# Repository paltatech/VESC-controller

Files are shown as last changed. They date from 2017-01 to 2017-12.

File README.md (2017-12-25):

# 3 phase motor controller for high power systems
This is the hardware repository of a 3 phase inverter brain, UNTESTED but designed with the following specs in mind:

* Compatible with VESC firmware and software tools
* Embedded security features (overcurrent protection, pwm overlap elimination, etc)


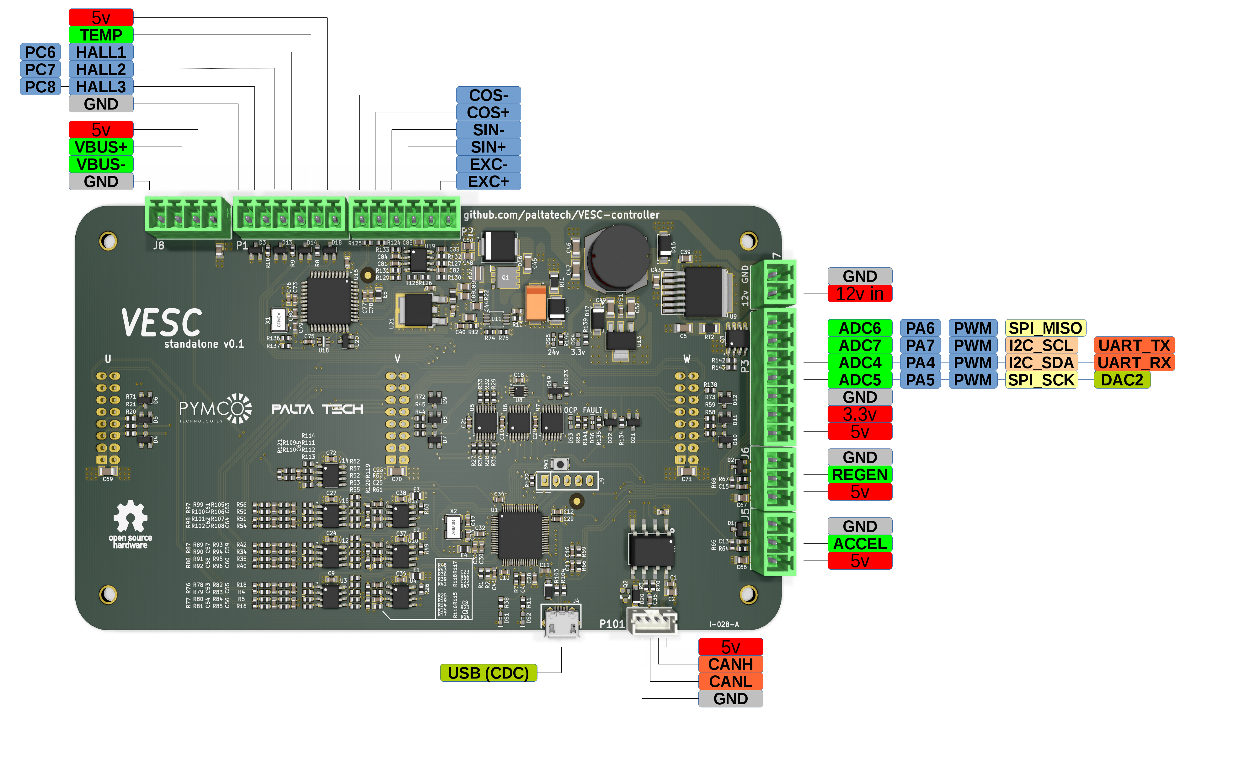
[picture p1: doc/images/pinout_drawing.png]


## Microcontroller
The core of the system is a 32 bit ARM Cortex M4 MCU (STM32F405) running ChibiOS RTOS.

## Communication interfaces
* CAN bus for control, configuration and monitoring
* USB for light usage, firmware upload/upgrade and configuration.
* UART, I2C and ADCs and GPIOs available

## Motor inputs
* Bus Voltage (differential)
* Phase current (differential)
* Phase voltage (differential)
* Gate driver fault
* Power_good from gate driver
* Motor temperature
* Hall/encoder
* Resolver

## Gate driver outputs
* PWM high/low
* dynamic gate drive current (pwm)
* 24v power

You can also check the layout [here](https://eyrie.io/board/6f397be723754f039735d8350260c2c0) 

Made open source with KiCAD, an open source EDA tool.

## Interface boards
This controller can be interfaced directly to a power stage, or through an interface board.
An example of interface board is at adaptor boards/power_integrations_2SP0115T2A/ and looks like this

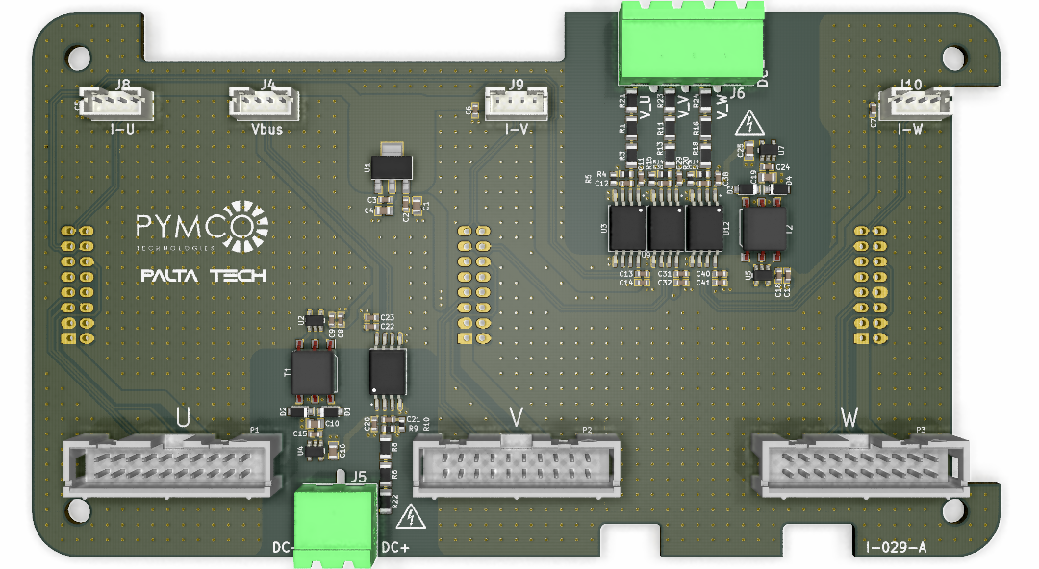
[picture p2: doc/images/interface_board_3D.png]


An example of system assembly is also included in this repository

## Control board setup

First you need to flash the VESC bootloader. To do so, connect a STLinkv2 to connector J9. In a Linux machine open a terminal and clone the bootloader repository:

1. `git clone git@github.com:vedderb/bldc-bootloader.git`
2. `cd bldc-bootloader`
3. `make upload`   <- this will compile and flash the bootloader

Next step is to flash the VESC firmware.

1. `git clone git@github.com:vedderb/bldc.git`
2. `Make sure you go to conf_general.h and uncomment the line #define HW_VERSION_PALTA. This will enable all the features especific to this high power control board.`
3. `Configure the DEADTIME required for your power switches, look for the line #define HW_DEAD_TIME_VALUE		181  // 1.4usec  in hw_palta.h`
4. `cd bldc`
5. `make upload`  <- this will compile and flash vesc firmware

Connect the board via USB (conn J4) and launch the latest [VESC-tool](http://vesc-project.com/vesc_tool).

1. Press the connect button (top right). The status bar should show your PALTA board connected.
2. Load a sample configuration for this board, you probably need to tune the deadtime compensation field.
3. Run the motor setup wizard.

## System setup

A high power controller would generally need a battery, wiring, contactor, DC link, gate drivers, switches, an interface board, 3 current sensors, a heatsink and a motor. Make sure you have everything you need and you understand all the connections and dangers involved, especially the safety related stuff.

## License
This documentation describes Open Hardware and is licensed under the CERN OHL v. 1.2

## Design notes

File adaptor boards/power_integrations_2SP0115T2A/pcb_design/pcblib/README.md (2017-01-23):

kicad-pcblib
============

(Warning: Work in progress!)

These are my KiCad PCB libraries, meant to be used with my schematic
libraries: https://github.com/cpavlina/kicad-schlib

IPC footprints
--------------

The IPC footprints are auto-generated from the FreePCB IPC libraries.
I used to require you to run 'make' to fetch them and convert them, but
FreePCB appears to be pretty solidly deceased now, so I'm including them
in my own library.

The FreePCB libraries are public domain (as clarified by FreePCB's creator,
contrary to the license of the software itself), and generated from IPC data.

If they ever do change and you want to rebuild them, here are the old instructions:

> Requires Make and Python 2.7+/3. Just run 'make ipc' after cloning this repository;
> the makefile will download the FreePCB IPC libraries and convert them to KiCad
> .pretty libs. Note that I am not distributing the FreePCB libraries, but I
> could; if they ever become unavailable I will add them here.

3D models
---------

The footprints reference [these nice 3D models](http://smisioto.no-ip.org/elettronica/kicad/kicad-en.htm).
There is a Python script to download and extract them; just run 'make 3d' to
run it.

They're pretty big, so please don't pull them repeatedly. Be nice to his server.

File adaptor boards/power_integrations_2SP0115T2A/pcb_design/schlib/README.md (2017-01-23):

kicad-schlib
============

(Warning: work in progress!)

These are my KiCad schematic libraries, meant to be used with my PCB
libraries:

https://github.com/cpavlina/kicad-pcblib

For preview renders, look here:

https://github.com/cpavlina/kicad-schlib-preview

Using these libraries
---------------------

This repository includes a script to create a KiCad project, at
[`create_project.sh`](https://raw.githubusercontent.com/cpavlina/kicad-schlib/master/create_project.sh),
to be called like this:

    create_project.sh  project_name

It will:

1. Create a directory called `project_name`
1. `git init` if not already in a git repository
1. Add `cpavlina/kicad-schlib` and `cpavlina/kicad-pcblib` as submodules, shallow-cloned to save space
1. Create the basic project files with all the libraries preloaded

The script doesn't depend on any other files in the repository, so you can
download and run only the script itself without having to clone the repository
yourself.

Why submodules?
---------------

Yeah, I know a lot of people don't like submods, but I find them just about
perfect for this application, for the following very important (IMHO) reason:

*Submodules link to a specific commit.* This is important when building a PCB.
KiCad does not version libraries, so without doing this, the libraries could
update underneath your project and introduce unnoticed errors. Using submodules
ties your project to the parts you initially started using, and if you want to
update (and have the time to review changes and make sure there are no errors),
you can do this manually.

When cloning a project using submodules, it is normally required to use `git
clone --recursive`; note that because KiCad cache the library parts that have
actually been used, a project will still be readable if the libraries aren't
also cloned (and can be distributed without them for reference purposes).

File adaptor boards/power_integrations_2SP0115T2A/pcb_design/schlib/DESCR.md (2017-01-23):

# Templates for part descriptions

## FPGA, CPLD, etc

`FPGA nLEs nIOs _RAM_ [footprint]`

`CPLD nLEs nIOs [footprint]`

- nLEs: Number of logic elements. `LEs:4608`
- nIOs: Number of IO pins. `IOs:142`
- RAM: Amount of RAM in metric kbits. `RAM:120kb`

These chips can differ significantly from each other, so just use common sense.

## A/D converters

`ADC.n nbit sps interface _inl_ _dnl_ _refppm_ [footprint]`

- sps: Samples per second. `50kSa/s` Alternatively: settling time. `15µs`
- interface: data interface (SPI, I2C, parallel, etc)
- inl: Integral nonlinearity, LSB. `INL:2`
- dnl: Differential nonlinearity, LSB. `DNL:3`
- refppm: PPM/K of integrated reference, if present. `Ref:2ppm/K`

## D/A converters

`DAC.n nbit sps interface _inl_ _dnl_ _refppm_ [footprint]`

- sps: Samples per second. `50kSa/s` Alternatively: settling time. `15µs`
- interface: data interface (SPI, I2C, parallel, etc)
- inl: Integral nonlinearity, LSB. `INL:2`
- dnl: Differential nonlinearity, LSB. `DNL:3`
- refppm: PPM/K of integrated reference, if present. `Ref:2ppm/K`

## Linear regulators, LDOs, DC-DC

`Reg Lin voltage current [footprint]`

`Reg LDO voltage current [footprint]`

`Reg Buck in:vin vout current freq [footprint]`

`Reg Boost in:vin vout current freq [footprint]`

Also RegCtrlr.

- voltage: output voltage or AdjV
- current: maximum output current or AdjI

The cutoff for linear vs. LDO is suggested to be a typical dropout of 1.2V at full load.
This places the worst IC commonly considered "LDO" (LM1117) just inside the LDO category.

## Voltage references

`VRef Series/Shunt voltage tolerance ppm/K [footprint]`

## Logarithmic amplifiers, detectors

`LogAmp dynamic_range bandwidth [footprint]`

`LogDetect dynamic_range bandwidth [footprint]`

The distiction is that detectors typically have an integrated low-pass filter, so
high RF comes out as a DC power level.

## Comparators

`Comp.n _delay_ _irange_ _outtech_ _extras_ [footprint]`

- .n: number of units. omit if one.
- delay: propagation delay, ns.
- irange: RRI, SSI, OverTopI
- outtech: OpenDrain, OpenColl, TTL, CMOS, LVDS, etc.
- extras: ProgHysteresis, etc.

## Operational amplifiers, instrumentation amplifiers

`OpAmp.n _intype_ GBW _slewrate_ _iorange_ _tech_ _extras_ [footprint]`

`InAmp.n _intype_ GBW _slewrate_ _iorange_ _tech_ _extras_ [footprint]`

- .n: number of units. omit if one.
- intype:
  - VFB for voltage feedback, but omit for GBW < 75 MHz
  - CFA for current feedback
- slewrate:
  - Only specify if notable (suggested cutoff: 6V * GBW)
  - Always specified in V/µs
- iorange:
  - RRI, RRO, RRI RRO if rail-to-rail (go by manufacturer's claims)
  - SSI, SSO, SSIO if single-supply
  - OverTopI if over-the-top
  - OpenCollO, OpenDrnO if open-collector/open-drain
- tech: input circuit technology. CMOS, JFET, etc. Omit for BJT or if unspecified.
- extras:
  - LowVos: low V offset (suggested: < 1mV)
  - VLowVos: very low V offset (suggested: < 50µV)
  - LowIB: low input bias current (suggested: < 1µA)
  - VLowIB: very low input bias current (suggested: < 1 nA)
  - LowNoise: low noise (cutoff depends on applications!)
  - Chopper: chopper-stabilized

## Discrete transistors

`PMOS.n _semi_ -xV -xA _Rdson_ _Vgsth_ [footprint]`

`NMOS.n _semi_ xV xA _Rdson_ _Vgsth_ [footprint]`

`PNP.n _semi_ -xV -xA _Pd_ _ft_ [footprint]`

`NPN.n _semi_ xV xA _Pd_ _ft_ [footprint]`

`NJF.n _semi_ xV Idss [footprint]`

`PJF.n _semi_ xV Idss [footprint]`

`SCR xV xA _Itsm_ [footprint]`

`PUT xV xW _Itrm_ [footprint]`

`UJT xV xW [footprint]`

- semi: specify semiconductor material for exotic devices
- Use negative voltage, current for P-type devices
- Rdson: on-resistance of MOSFET. `34mR`
- Vgsth: threshold of MOSFET. Typically at a low current like 250µA. Negative for P-type. `-3Vth`

## Discrete diodes

`Diode xV xA [footprint]`

`Schottky xV xA [footprint]`

`Zener xV xW Iz:xA [footprint]`

`TVS xV _pulse_ _Cj_ [footprint]`

`Varicap xV Cjrange [footprint]`

`LED color wavelength xV xA [footprint]`

- pulse: 8/20µs peak pulse

## Optocouplers

`Optocoup NPN+base isoV fwdcurrentA vvvVceo [footprint]`

## Microcontrollers

`MCU nbit/arch ROM:nKB RAM:nKB _extras_ [footprint]`

- arch: for ARM, use such as ARM-M4
- extras: list features not including the usuals like SPI/I2C/UART.

## Passives

`IND nH nR _SRF:100MHz_ _(dimensions)_ _[footprint]_`

## Digital interface converters

`Interface FROM TO [footprint]`

## Digital attenuators

`Atten ndB nbit BW _tech_ [footprint]`

- tech: device/semiconductor technology, if appropriate

## Analog switch

`AnSwitch nPnT _tech_ _extras_ [footprint]`

## Memories

`Mem type size interface _speed_ [footprint]`

- type: EEPROM, Flash, SRAM, DRAM, DDR2-SDRAM, etc
- size: use B for byte, bit for bit
- speed: either interface clock or access time

## Temperature sensors

`Sensor Temp range accuracy interface [footprint]`

- range: only specified range (not absolute max): `0-70C`
- accuracy: `±2C`
- interface: can be `Analog`

## Digital drivers, level shifters, translators

`Logic BusTXRX width supplyrange/techs speed features [footprint]`

`Logic LevelShift width supplyrange/techs speed features [footprint]`

`Logic TXRX supplyrange/techs speed features [footprint]`

`Logic TX supplyrange/techs speed features [footprint]`

`Logic RX supplyrange/techs speed features [footprint]`

`Logic Isolator supplyrange speed isolation features [footprint]`

## Oscillators, PLL

`Osc freq _tech_ outtype extras [footprint]`

`PLL freqmax outtype extras [footprint]`

`OscPLL freqmax outtype extras [footprint]`

- tech: oscillator technology (Crystal, CMEMS, etc)

## Power drivers

`Driver type nchannels tech powerlevel interface [footprint]`

## Displays

`Display VFD 7seg Digits:8 Muxed`

`Display LED 7seg Digits:3 Muxed Green`

## Modulators, Demodulators

`ModDemod freq (type) [footprint]`

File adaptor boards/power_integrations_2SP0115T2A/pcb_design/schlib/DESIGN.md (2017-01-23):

# Design Guidelines

## General

- Descriptions are standardized for simple searching. See DESCR.md. If you want to add a new class of part that doesn't have an entry in DESCR.md, please contribute to that file as well.
- Separate power units: orient vertically, pins at +/- 0.4in with 0.15in length
- Text should be 50 mil in general
- Pin length, numbering, general naming:

    - ICs: pins at least 0.15in long, pin numbers 50 mil text
    - Discrete semis: pin numbers 40 mil text.
    - Passives: omit pin numbers for two-pin parts. Three-pin parts can omit numbers when the third pin is structural (e.g. grounded crystal). When using numbers, use 40 mil text.
    - Name all pins. Hide names when the symbol graphic identifies the pin instead (transistor BCE, etc)
    - Prefer overbar for inverted pins with names, inversion circle for inverted pins without names. Don't combine the two!

- In manufacturer libraries, name parts according to manufacturer naming scheme.
- One footprint per part; specify footprint in Footprint field
- For parts with a large number of variants (e.g. fixed-voltage regulators), a placeholder in the name is acceptable: LM1117DT-v.v
- Prefer logical schematic to blank parts with names - e.g., use buffer symbol in buffers, not just pins named IN and OUT.
- Include [bomtool](https://github.com/cpavlina/bomtool) BOM lines whenever possible.
- Do not duplicate data! Don't fill in footprint filters, we use the footprint *field*. Don't use the keywords field, the new component chooser filters on description.

## Power supply naming

- Do not follow manufacturer naming. Be consistent, Microchip's "VSS" is no different from Atmel's "GND".
- For single rail parts, name main supply V+ (not VCC, VDD)
- For multi-rail parts, name main supply according to use when possible (VCORE, not V1.2)
- Ground is GND, not VSS

## Template parts

- Template libraries are prefixed with an underscore (`_passive`, `_semi`)
- Do not include footprints

## Very large logic (FPGA, large MCU, etc)

- Use "bracketed" multi-part style (see Altera library for an example)

## Small logic (7400, etc)

- Use traditional (non-IEC) symbols for very simple like NAND
- Use IEC or IEC-like symbols for more complex like shift register
- Use separate power units

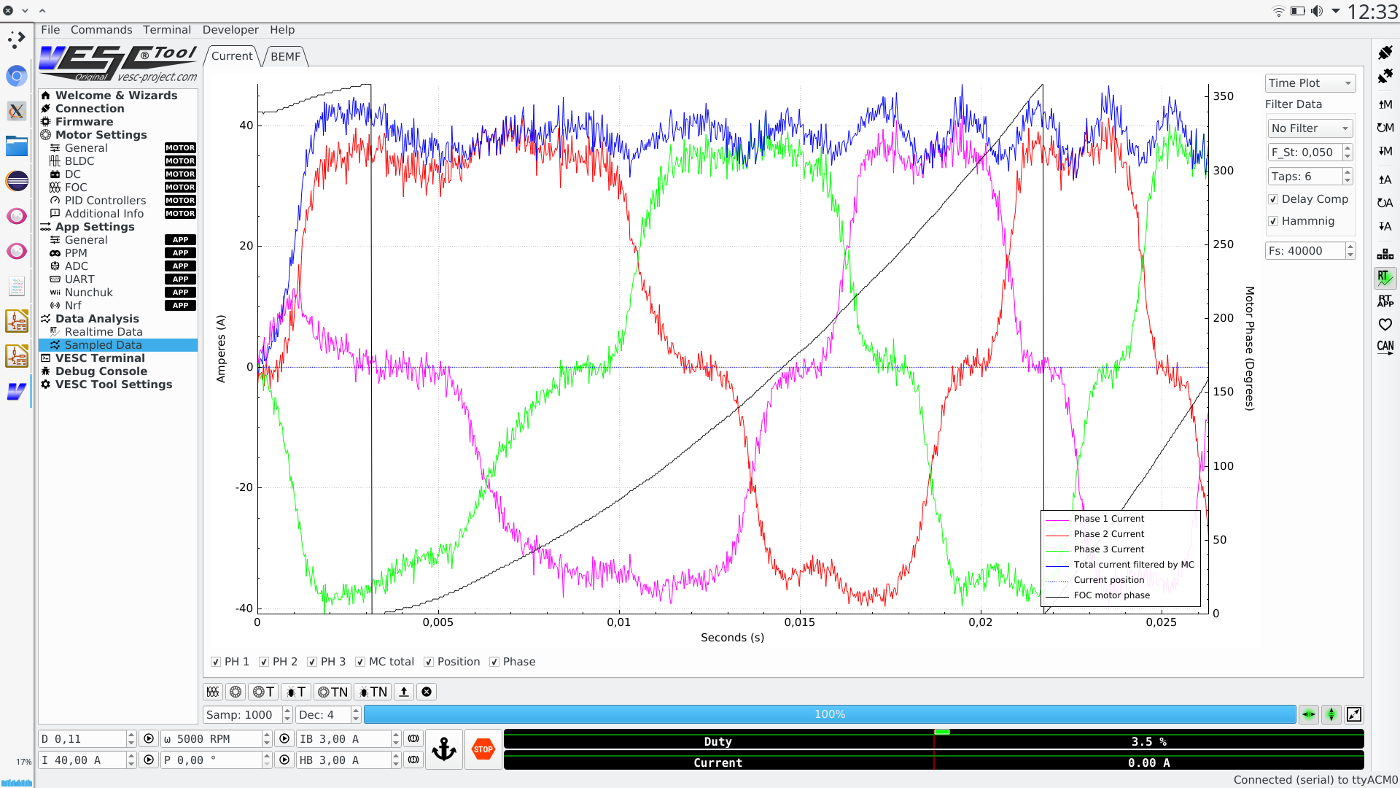
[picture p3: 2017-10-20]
adaptor boards/power_integrations_2SP0115T2A/doc/startup with 1.4usec DT.png

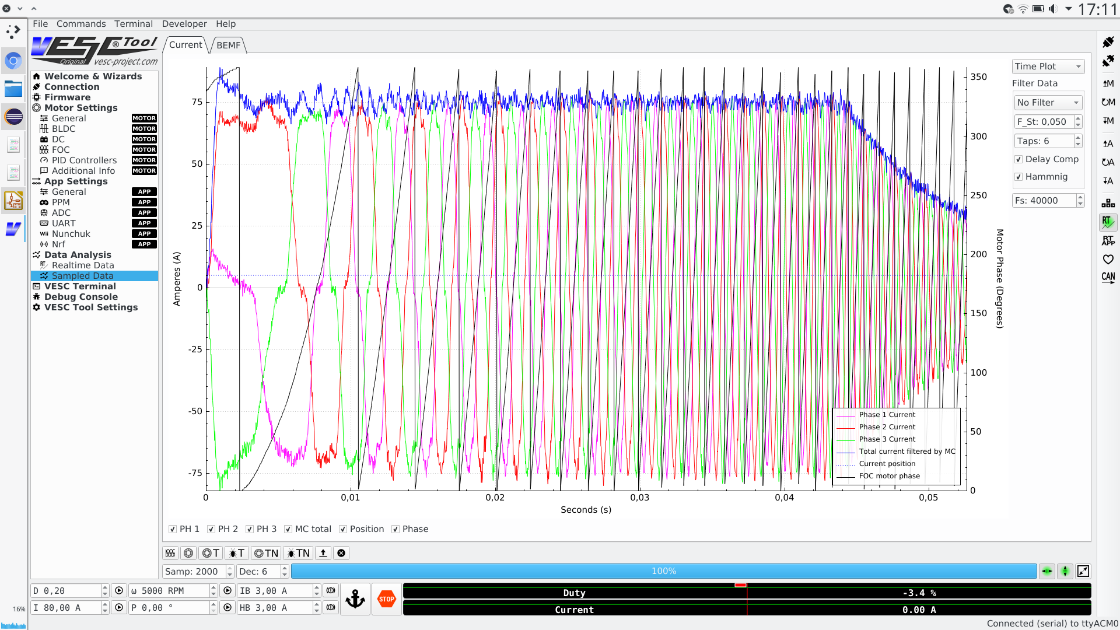
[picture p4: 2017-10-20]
adaptor boards/power_integrations_2SP0115T2A/doc/startup with 1.4usec DT 80A.png

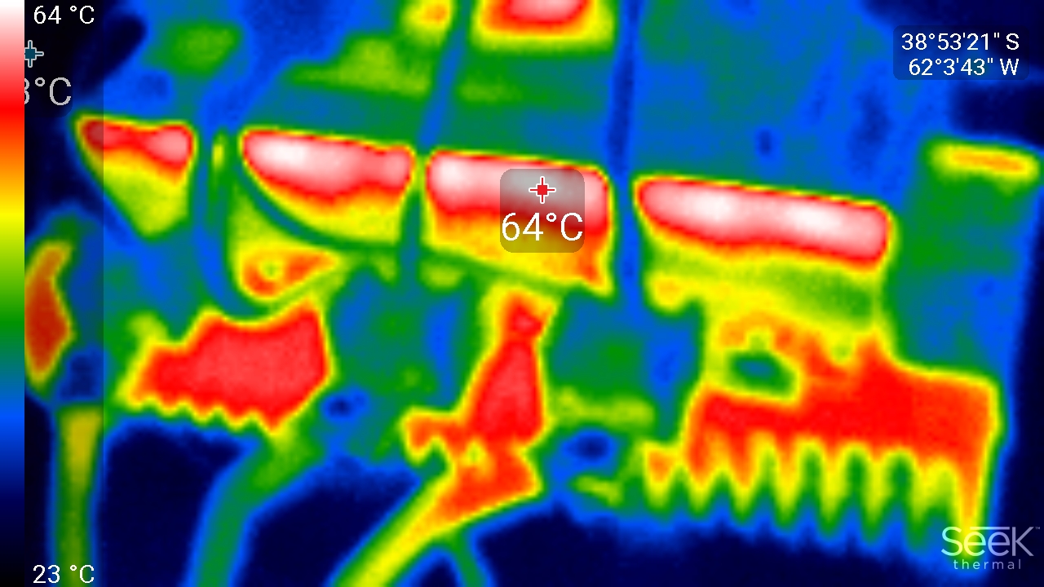
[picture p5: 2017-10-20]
adaptor boards/power_integrations_2SP0115T2A/doc/img_thermal_1497133271852.jpg

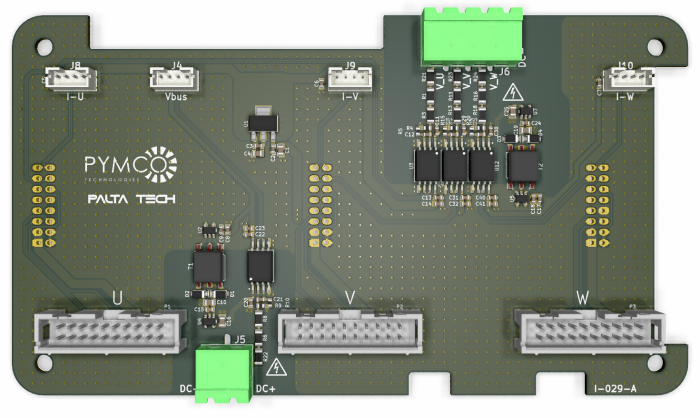
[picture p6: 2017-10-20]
adaptor boards/power_integrations_2SP0115T2A/doc/interface board v0.1.png

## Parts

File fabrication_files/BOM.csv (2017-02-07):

Refs | Value | Footprint | QTY | MFR | MPN | SPR | SPN
RT1 | FUSE 5A SLOW | IPC7351-Most:RESC3216X60 | 1 | Bel Fuse Inc. | C1S 5 | Digikey | 507-1194-1-ND
RT2 | POLYFUSE 1A | IPC7351-Most:RESC3216X60 | 1 | Bel Fuse Inc. | 0ZCJ0050AF2E | Digikey | 507-1803-1-ND
C401;C1;C35;C18;C21;C20;C19;C74;C73;C77;C82;C81;C85;C75;C87;C86;C51;C13;C13;C32;C30;C34;C10;C11;C12;C3;C9;C36;C3;C9;C36;C3;C9;C36;C72 | 100nF | IPC7351-Nominal:CAPC1608X55 | 35 | Murata Electronics North America | GRM188R71E104KA01D | Digikey | 490-1524-1-ND
C8;C8;C8;C65 | 100pF | IPC7351-Nominal:CAPC1608X55 | 4 | KEMET | C0603C101J5GACTU | Digikey | 399-1061-1-ND
C83;C84 | 120pF | IPC7351-Nominal:CAPC1608X55 | 2 | KEMET | C0603C121F5GACTU | Digikey | 399-7850-1-ND
C79;C80;C17;C33 | 15pF | IPC7351-Nominal:CAPC1608X55 | 4 | Murata Electronics North America | GCM1885C1H150JA16D | Digikey | 490-4957-1-ND
C40;C42 | 180nF | IPC7351-Nominal:CAPC1608X55 | 2 | Murata Electronics North America | GRM188R71E184KA88D | Digikey | 490-6431-1-ND
C14;C14 | 1nF | IPC7351-Nominal:CAPC1608X55 | 2 | Murata Electronics North America | GRM188R71H102KA01D | Digikey | 490-1494-1-ND
C53;C54;C53;C54;C53;C54 | 2.2nF | IPC7351-Nominal:CAPC1608X55 | 6 | Murata Electronics North America | GRM188R71H222KA01D | Digikey | 490-1500-1-ND
C76;C78;C41;C31;C28;C29;C4 | 2.2uF | IPC7351-Nominal:CAPC1608X55 | 7 | Murata Electronics North America | GRM188R71A225KE15D | Digikey | 490-4520-1-ND
C55;C56;C55;C56;C55;C56 | 220pF | IPC7351-Nominal:CAPC1608X55 | 6 | Murata Electronics North America | GRM1885C1H221JA01D | Digikey | 490-1435-1-ND
R37 | 18mOhm | IPC7351-Nominal:CAPC1632X76 | 1 | Susumu | PRL1632-R018-F-T1 | Digikey | PRL1632.018FCT-ND
C39;C43 | 1uF 50v | IPC7351-Nominal:CAPC2012X70 | 2 | Taiyo Yuden | UMK212B7105KG-T | Digikey | UMK212B7105KG-T
C88;C89;C48;C50 | 22uF | IPC7351-Nominal:CAPC2012X70 | 4 | TDK Corporation | C2012X5R1V226M125AC | Digikey | 445-14428-1-ND
C2;C68;C66;C67 | 4.7uF | IPC7351-Nominal:CAPC2012X70 | 4 | Murata Electronics North America | GRM21BR71A475KA73K | Digikey | 490-6479-1-ND
C44 | 680pF | IPC7351-Nominal:CAPC2012X70 | 1 | Samsung Electro-Mechanics America, Inc. | CL21C751JBCNNNC | Digikey | 1276-2691-1-ND
C7 | 750pF | IPC7351-Nominal:CAPC2012X70 | 1 | Samsung Electro-Mechanics America, Inc. | CL21C751JBCNNNC | Digikey | 1276-2691-1-ND
C5 | 10uF 35v | IPC7351-Nominal:CAPC3216X70 | 1 | Taiyo Yuden | GMK316AB7106KL-TR | Digikey | 587-3007-1-ND
C45 | 2.2uF 50v | IPC7351-Nominal:CAPC3216X70 | 1 | Murata Electronics North America | GRM31CR71H225KA88L | Digikey | 490-3367-1-ND
C46;C47;C49;C52 | 22uF 10v | IPC7351-Nominal:CAPC3216X70 | 4 | Taiyo Yuden | LMK316AB7226ML-TR | Digikey | 587-2782-1-ND
C71;C70;C69 | 4.7uF 50v | IPC7351-Nominal:CAPC3216X70 | 3 | Murata Electronics North America | GRM31CR71H475KA12L | Digikey | 490-6521-1-ND
C6 | 4.7uF 50v tant | IPC7351-Nominal:CAPMP7343X310 | 1 | Vishay Sprague | 593D475X9050D2TE3 | Digikey | 718-1107-1-ND
D15;D17 | SS16 | IPC7351-Nominal:DIOM5326X292 | 2 | Fairchild/ON Semiconductor | SS16 | Digikey | SS16FSCT-ND
D16 | 30BQ100TR | IPC7351-Nominal:DIOM7959X265 | 1 | SMC Diode Solutions | 30BQ100TR | Digikey | 1655-1389-1-ND
E5;E6;E4;E1;E1;E1 | BEAD-220ohm@100khz | IPC7351-Nominal:INDC2012X130 | 6 | Murata Electronics North America | BLM21PG221SN1D | Digikey | 490-1054-1-ND
L1;L3 | 22uH 5.2A | IPC7351-Nominal:INDC3225X135 | 2 | Bourns Inc. | SRR1210-220M | Digikey | SRR1210-220MCT-ND
X1;X2 | ABM3B - 8MHz | IPC7351-Nominal:OSCCC320X500X150 | 2 | Abracon LLC | ABM3B-8.000MHZ-10-1UT | Digikey | 535-9721-1-ND
U1 | STM32F40X_LQFP64 | IPC7351-Nominal:QFP50P1200X1200X100-64 | 1 | STMicroelectronics | STM32F405RGT6 | Digikey | 497-11767-ND
U15 | AD2S1205 | IPC7351-Nominal:QFP80P1200X1200X160-44 | 1 | Analog Devices Inc. | AD2S1205YSTZ | Digikey | AD2S1205YSTZ-ND
R136;R137;R6 | 0R | IPC7351-Nominal:RESC1608X50 | 3 | Yageo | RC0603JR-070RL | Digikey | 311-0.0GRCT-ND
R12 | 1.78k | IPC7351-Nominal:RESC1608X50 | 1 | Yageo | RC0603FR-071K78L | Digikey | 311-1.78KHRCT-ND
R86;R141;R22;R78;R79;R80;R81;R78;R79;R80;R81;R38;R11;R135;R134;R78;R79;R80;R81 | 100R | IPC7351-Nominal:RESC1608X50 | 19 | Yageo | RC0603FR-07100RL | Digikey | 311-100HRCT-ND
R65;R65 | 100k | IPC7351-Nominal:RESC1608X50 | 2 | Yageo | RC0603FR-07100KL | Digikey | 311-100KHRCT-ND
R138;R126;R130;R128;R131;R75;R143;R142;R2;R10;R9;R8;R7;R18;R16;R19;R17;R25;R24;R18;R16;R19;R17;R25;R24;R140;R18;R16;R19;R17;R25;R24;R111;R112;R114;R113 | 10k | IPC7351-Nominal:RESC1608X50 | 36 | Yageo | RC0603FR-0710KL | Digikey | 311-10.0KHRCT-ND
R132;R133 | 15.4k | IPC7351-Nominal:RESC1608X50 | 2 | Yageo | RC0603FR-0715K4L | Digikey | 311-15.4KHRCT-ND
R74 | 180k | IPC7351-Nominal:RESC1608X50 | 1 | Yageo | RC0603FR-07180KL | Digikey | 311-180KHRCT-ND
R64;R64;R122;R23;R82;R83;R84;R85;R116;R115;R23;R82;R83;R84;R85;R116;R115;R139;R23;R82;R83;R84;R85;R116;R115 | 1k | IPC7351-Nominal:RESC1608X50 | 25 | Yageo | RC0603FR-071KL | Digikey | 311-1.00KHRCT-ND
R123;R20;R21;R71;R20;R21;R71;R103;R104;R20;R21;R71 | 22R | IPC7351-Nominal:RESC1608X50 | 12 | Yageo | RC0603FR-0722RL | Digikey | 311-22.0HRCT-ND
R127;R129 | 22k | IPC7351-Nominal:RESC1608X50 | 2 | Yageo | RC0603FR-0722KL | Digikey | 311-22.0KHRCT-ND
R66;R66 | 270k | IPC7351-Nominal:RESC1608X50 | 2 | Yageo | RC0603FR-07270KL | Digikey | 311-270KHRCT-ND
R76;R77;R76;R77;R76;R77;R121 | 2k | IPC7351-Nominal:RESC1608X50 | 7 | Yageo | RC0603FR-072KL | Digikey | 311-2.00KHRCT-ND
R13 | 33.2k | IPC7351-Nominal:RESC1608X50 | 1 | Yageo | RC0603FR-0733K2L | Digikey | 311-33.2KHRCT-ND
R30;R27;R31;R28;R32;R29;R33;R26;R26;R26;R109;R110 | 4.7k | IPC7351-Nominal:RESC1608X50 | 12 | Yageo | RC0603FR-074K7L | Digikey | 311-4.70KHRCT-ND
R3;R70 | 60.4R | IPC7351-Nominal:RESC1608X50 | 2 | Yageo | RC0603FR-0760R4L | Digikey | 311-60.4HRCT-ND
R124;R125 | 68.1k | IPC7351-Nominal:RESC1608X50 | 2 | Yageo | RC0603FR-0768K1L | Digikey | 311-68.1KHRCT-ND
R4;R5;R14;R15;R4;R5;R14;R15;R4;R5;R14;R15 | 8.87k | IPC7351-Nominal:RESC1608X50 | 12 | Yageo | RC0603FR-078K87L | Digikey | 311-8.87KHRCT-ND
R1 | NTC 10k | IPC7351-Nominal:RESC1608X50 | 1 | Murata Electronics North America | NCP18XH103F03RB | Digikey | 490-4800-1-ND
U19 | AD8397 | IPC7351-Nominal:SOIC127P600X175-8 | 1 | Analog Devices Inc. | AD8397ARZ | Digikey | AD8397ARZ-ND
Q3 | AO4805 | IPC7351-Nominal:SOIC127P600X175-8 | 1 | Alpha & Omega Semiconductor Inc. | AO4805 | Digikey | 785-1055-1-ND
U4;U4;U4 | LM2903DT | IPC7351-Nominal:SOIC127P600X175-8 | 3 | STMicroelectronics | LM2903DT | Digikey | 497-1559-1-ND
U3;U3;U3;U14 | OPA2376AIDR | IPC7351-Nominal:SOIC127P600X175-8 | 4 | Texas Instruments | OPA2376AIDR | Digikey | 296-22564-1-ND
U8 | SN74AUP1G74 | IPC7351-Nominal:SOP50P310X100-8 | 1 | Texas Instruments | SN74AUP1G74DCUR | Digikey | 296-19761-1-ND
U11 | LM3488 | IPC7351-Nominal:SOP65P490X109-8 | 1 | Texas Instruments | LM3488MM/NOPB | Digikey | LM3488MM/NOPBCT-ND
U5 | 7400-TSSOP | IPC7351-Nominal:SOP65P640X110-14 | 1 | Texas Instruments | SN74LVC00APWR | Digikey | 296-1216-1-ND
U6;U7 | SN74ACT08PWR | IPC7351-Nominal:SOP65P640X110-14 | 2 | Texas Instruments | SN74ACT08PWR | Digikey | 296-4355-1-ND
J9 | SWD | conn-100mil:CONN-100MIL-M-1x5 | 1
J1 | GATE_DRIVER_CONN_U | conn-100mil:CONN-100MIL-M-2x8 | 1 | Amphenol FCI | 67997-216HLF | Digikey | 609-3238-ND
J2 | GATE_DRIVER_CONN_V | conn-100mil:CONN-100MIL-M-2x8 | 1 | Amphenol FCI | 67997-216HLF | Digikey | 609-3238-ND
J3 | GATE_DRIVER_CONN_W | conn-100mil:CONN-100MIL-M-2x8 | 1 | Amphenol FCI | 67997-216HLF | Digikey | 609-3238-ND
J4 | micro USB | conn-fci:CONN-10118194-0001LF-FCI | 1 | Amphenol FCI | 10118194-0001LF | Digikey | 609-4618-1-ND
J7 | 12V | conn-phoenix:mcv_1,5-2-G-3,81 | 1 | Phoenix Contact | 1803426 | Digikey | 277-1221-ND
J5 | ACCEL | conn-phoenix:mcv_1,5-3-G-3,81 | 1 | Phoenix Contact | 1803439 | Digikey | 277-1222-ND
J6 | REGEN | conn-phoenix:mcv_1,5-3-G-3,81 | 1 | Phoenix Contact | 1803439 | Digikey | 277-1222-ND
J8 | V_BUS | conn-phoenix:mcv_1,5-4-G-3,81 | 1 | Phoenix Contact | 1803442 | Digikey | 277-1223-ND
P1 | HALL/Encoder | conn-phoenix:mcv_1,5-6-G-3,81 | 1 | Phoenix Contact | 1803468 | Digikey | 277-1225-ND
P2 | Resolver | conn-phoenix:mcv_1,5-6-G-3,81 | 1 | Phoenix Contact | 1803468 | Digikey | 277-1225-ND
P3 | PWR_COMM | conn-phoenix:mcv_1,5-7-G-3,81 | 1 | Phoenix Contact | 1803471 | Digikey | 277-1226-ND
L2 | 27uH | manuf:BOURNS-SDR1307 | 1 | Bourns Inc. | SDR1307-270ML | Digikey | SDR1307-270MLCT-ND
Q1 | BSC340N08 | manuf:TEXAS-Q5A | 1 | Infineon Technologies | BSC340N08NS3GATMA1 | Digikey | BSC340N08NS3GATMA1CT-ND
U9 | LM22676QTJ-5.0 | manuf:TO-263-7-TEXAS | 1 | Texas Instruments | LM22676QTJE-5.0/NOPB | Digikey | LM22676QTJE-5.0/NOPBCT-ND
SW1 | BOOTLOADER | paltatech:SMD-Switch_B3U-1000-B | 1 | Omron Electronics Inc-EMC Div | B3U-1000P | Digikey | SW1020CT-ND
U2 | ISO1050 | paltatech:SO8-ISO1050 | 1 | Texas Instruments | ISO1050DUBR | Digikey | 296-24818-1-ND
DS6 | FAULT | smd-semi:LED-0603 | 1 | Lite-On Inc. | LTST-C191KRKT | Digikey | 160-1447-1-ND
DS2;DS4 | GREEN | smd-semi:LED-0603 | 2 | Lite-On Inc. | LTST-C191KGKT | Digikey | 160-1446-1-ND
DS3 | OCP | smd-semi:LED-0603 | 1 | Lite-On Inc. | LTST-C191KRKT | Digikey | 160-1447-1-ND
DS1;DS5 | RED | smd-semi:LED-0603 | 2 | Lite-On Inc. | LTST-C191KRKT | Digikey | 160-1447-1-ND
Q2 | 2N7002PW | smd-semi:SC-70 | 1 | Nexperia USA Inc. | 2N7002PW,115 | Digikey | 568-5987-1-ND
U18 | SN74LVC1G | smd-semi:SC-70-6 | 1 | Texas Instruments | SN74LVC1G11IDCKRQ1 | Digikey | 296-36722-1-ND
D20 | MBR0540 | smd-semi:SOD-123 | 1 | Fairchild/ON Semiconductor | MBR0540 | Digikey | MBR0540CT-ND
U13 | LM1117IMP-v.v | smd-semi:SOT-223 | 1 | Texas Instruments | LM1117IMP-3.3/NOPB | Digikey | LM1117IMP-3.3/NOPBCT-ND
U20 | APX809 | smd-semi:SOT-23 | 1 | Diodes Incorporated | APX809-46SRG-7 | Digikey | APX809-46SRGDICT-ND
D19;D1;D1;D3;D13;D14;D18;D4;D5;D6;D4;D5;D6;D22;D21;D4;D5;D6 | BAT54S | smd-semi:SOT-23 | 18 | Toshiba Semiconductor and Storage | TBAT54S,LM | Digikey | TBAT54SLMCT-ND
U21 | NCV78Mxx | smd-semi:TO-252 | 1 | ON Semiconductor | NCV78M12BDTRKG | Digikey | NCV78M12BDTRKGOSCT-ND
P101 | CANBUS | w_conn_jst-ph:b4b-ph-kl | 1 | JST Sales America Inc. | B4B-PH-K-S(LF)(SN) | Digikey | 455-1706-ND
DZ1 | 1SMB18CAT | w_smd_diode:do214aa | 1 | ON Semiconductor | 1SMB18CAT3G | Digikey | 1SMB18CAT3GOSCT-ND

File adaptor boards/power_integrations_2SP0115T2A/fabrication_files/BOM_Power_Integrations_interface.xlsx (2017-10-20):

 |  |  |  |  |  |  | Board Qty: | 10
 |  |  |  |  |  |  | Total Cost: | $1107.35 |  |  |  | $547.41 |  |  |  |  |  | $442.05 |  |  |  |  |  | $892.66 |  |  |  |  |  | $507.91 |  |  |  |  |  | $2786.40
 |  |  |  |  |  |  | Unit Cost: | $110.74
Global Part Info |  |  |  |  |  |  |  |  | Digi-Key |  |  |  |  |  | Farnell |  |  |  |  |  | Mouser |  |  |  |  |  | Newark |  |  |  |  |  | Rs Components
Refs | Value | Desc | Footprint | Manf | Manf# | Qty | Unit$ | Ext$ | Avail | Purch | Unit$ | Ext$ | Cat# | Doc | Avail | Purch | Unit$ | Ext$ | Cat# | Doc | Avail | Purch | Unit$ | Ext$ | Cat# | Doc | Avail | Purch | Unit$ | Ext$ | Cat# | Doc | Avail | Purch | Unit$ | Ext$ | Cat# | Doc
P1-P3 | 2SP0115T_conector |  | conn-100mil:CONN-100MIL-F-2x10 | Amphenol FCI | 75869-104LF | 30 | $0.97 | $29.21 | 1894 |  | $1.20 | $35.85 | 609-1776-ND | Link (http://www.digikey.com/scripts/DkSearch/dksus.dll?WT.z_header=search_go&lang=en) |  |  | $0.97 | $29.21 | 1103952 | Link (http://it.farnell.com/webapp/wcs/stores/servlet/Search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) | 481 |  | $1.08 | $32.40 | 649-75869-104LF | Link (http://www.mouser.com/Search/Refine.aspx?Keyword=75869-104LF%20) |  |  | $1.01 | $30.30 | 93K5090 | Link (http://www.newark.com/webapp/wcs/stores/servlet/Search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) | 150 |  | $1.00 | $29.98 | 673-7600 | Link (http://it.rs-online.com/web/c/?searchTerm=75869-104LF%20)
R2,R7,R12,R17 | 20k |  | IPC7351-Nominal:RESC6432X70 |  | CRCW251220K0JNEG | 40 | $0.13 | $5.10 | 12547 |  | $0.35 | $13.92 | 541-20KXCT-ND | Link (http://www.digikey.com/product-detail/en/vishay-dale/CRCW251220K0JNEG/541-20KXCT-ND/1178612) |  |  | $0.17 | $6.93 | 1571740 | Link (http://it.farnell.com/webapp/wcs/stores/servlet/Search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) | 1615 |  | $0.22 | $8.64 | 71-CRCW2512J-20K-E3 | Link (http://www.mouser.com/ProductDetail/Vishay/CRCW251220K0JNEG/) |  |  | $0.18 | $7.40 | 89M6939 | Link (http://www.newark.com/webapp/wcs/stores/servlet/Search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) |  |  | $0.13 | $5.10 | 842-9496 | Link (http://it.rs-online.com/web/c/?searchTerm=CRCW251220K0JNEG%20)
U3,U6,U9,U12 | AMC1301 |  | IPC7351-Nominal:SOIC127P1032X265-8 | Texas Instruments | AMC1301DWVR | 40 | $5.65 | $226.04 | 3988 |  | $5.65 | $226.04 | 296-44577-1-ND | Link (http://www.digikey.com/product-detail/en/texas-instruments/AMC1301DWVR/296-44577-1-ND/6131178) |  |  | $5.74 | $229.61 | 2617071 | Link (http://it.farnell.com/texas-instruments/amc1301dwvr/amp-isolamento-210khz-50uv-soic/dp/2617071) |  |  |  |  |  |  |  |  | $7.03 | $281.20 | 96Y8999 | Link (http://www.newark.com/webapp/wcs/stores/servlet/Search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)
C11,C20,C29,C38 | 100nF |  | IPC7351-Nominal:CAPC1608X55 | Murata Electronics North America | GRM188R71E104KA01D | 40 | $0.02 | $0.77 | 9708975 |  | $0.09 | $3.44 | 490-1524-1-ND | Link (http://www.digikey.com/product-detail/en/murata-electronics-north-america/GRM188R71E104KA01D/490-1524-1-ND/587865) |  |  |  |  | 1828899 | Link (http://it.farnell.com/murata/grm188r71e104ka01d/condensatore-mlcc-x7r-100nf-25v/dp/1828899) |  |  |  |  |  |  |  |  |  |  | 14T3317 | Link (http://www.newark.com/murata/grm188r71e104ka01d/capacitor-ceramic-0-1uf-10-25v/dp/14T3317) |  |  | $0.02 | $0.77 | 723-5638 | Link (http://it.rs-online.com/web/c/?searchTerm=GRM188R71E104KA01D%20)
U4,U7 | TPS76350 |  | smd-semi:SOT-23-5 | Texas Instruments | TPS76350DBVR | 20 | $0.76 | $15.26 | 2878 |  | $0.86 | $17.14 | 296-2707-1-ND | Link (http://www.digikey.com/product-detail/en/texas-instruments/TPS76350DBVT/296-2707-1-ND/381498) |  |  | $0.81 | $16.22 | 2764732 | Link (http://it.farnell.com/webapp/wcs/stores/servlet/Search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) |  |  |  |  |  |  |  |  | $0.76 | $15.26 | 77C1037 | Link (http://www.newark.com/webapp/wcs/stores/servlet/Search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) |  |  |  |  | 661-4242 | Link (http://it.rs-online.com/web/p/regolatori-di-tensione-low-dropout/6614242/)
J3 | GATE_DRIVER_CONN_W |  | conn-100mil:CONN-100MIL-M-2x8 | Amphenol FCI | 87606-308LF | 10 | $1.77 | $17.70 | 1177 |  | $1.97 | $19.65 | 609-3554-ND | Link (http://www.digikey.com/scripts/DkSearch/dksus.dll?WT.z_header=search_go&lang=en) |  |  | $2.00 | $19.98 | 1278235 | Link (http://it.farnell.com/webapp/wcs/stores/servlet/Search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) | 346 |  | $1.77 | $17.70 | 649-87606-308LF | Link (http://www.mouser.com/Search/Refine.aspx?Keyword=87606-308LF%20) |  |  | $1.92 | $19.20 | 63K0748 | Link (http://www.newark.com/webapp/wcs/stores/servlet/Search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) |  |  | $1.83 | $18.29 | 859-9488 | Link (http://it.rs-online.com/web/c/?searchTerm=87606-308LF%20)
J4 | VBUS |  | w_conn_jst-ph:b4b-ph-kl | JST Sales America Inc. | B4B-PH-K-S(LF)(SN) | 10 | $0.14 | $1.42 | 77385 |  | $0.23 | $2.27 | 455-1706-ND | Link (http://www.digikey.com/scripts/DkSearch/dksus.dll?WT.z_header=search_go&lang=en) |  |  | $0.14 | $1.42 | 9492437 | Link (http://it.farnell.com/webapp/wcs/stores/servlet/Search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) |  |  |  |  | Not Assigned | Link (http://www.mouser.com/ProductDetail/JST-Automotive/B4B-PH-K-S-LFSNP/) |  |  | $0.23 | $2.32 | 37K9958 | Link (http://www.newark.com/webapp/wcs/stores/servlet/Search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) | 740 |  | $0.17 | $1.66 | 820-1434 | Link (http://it.rs-online.com/web/p/file-di-contatti-da-pcb/8201434/)
J6 | Phoenix 1757268 5.08mm |  | w_conn_screw:mstba_2,5%2f4-g-5,08 | Phoenix Contact | 1757268 | 10 | $0.56 | $5.62 |  |  |  |  |  |  |  |  | $0.56 | $5.62 | 3705195 | Link (http://it.farnell.com/webapp/wcs/stores/servlet/Search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) | 2637 |  | $1.23 | $12.30 | 651-1757268 | Link (http://www.mouser.com/ProductDetail/Phoenix-Contact/1757268/?qs=sGAEpiMZZMuVJC7Vq%252bMl52CI6Cmc3FQC) |  |  | $1.21 | $12.10 | 71C4163 | Link (http://www.newark.com/webapp/wcs/stores/servlet/Search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) | 240 |  | $0.75 | $7.55 | 189-6127 | Link (http://it.rs-online.com/web/c/?searchTerm=1757268%20)
D2,D4 | MBR0520 |  | smd-semi:SOD-123 | ON Semiconductor | MBR0520LT1G | 20 | $0.05 | $0.94 |  |  | $0.30 | $6.00 | MBR0520LT1GOSCT-ND | Link (http://www.digikey.com/product-detail/en/on-semiconductor/MBR0520LT1G/MBR0520LT1GOSCT-ND/917965) |  |  | $0.11 | $2.13 | 9556915 | Link (http://it.farnell.com/on-semiconductor/mbr0520lt1g/diodo-schottky-0-5a-20v-smc/dp/9556915) |  |  |  |  |  |  |  |  | $0.05 | $0.94 | 94W8549 | Link (http://www.newark.com/on-semiconductor/mbr0520lt1g/rectifier-diode-single-20-v-500/dp/94W8549) |  |  | $0.09 | $1.74 | 463-432 | Link (http://it.rs-online.com/web/p/diodi-rettificatori-e-schottky/0463432/)
D1,D3 | MBR0520 |  | smd-semi:SOD-123 | ON Semiconductor | MBR0520LT1G | 20 | $0.05 | $0.94 |  |  | $0.30 | $6.00 | MBR0520LT1GOSCT-ND | Link (http://www.digikey.com/product-detail/en/on-semiconductor/MBR0520LT1G/MBR0520LT1GOSCT-ND/917965) |  |  | $0.11 | $2.13 | 9556915 | Link (http://it.farnell.com/on-semiconductor/mbr0520lt1g/diodo-schottky-0-5a-20v-smc/dp/9556915) |  |  |  |  |  |  |  |  | $0.05 | $0.94 | 94W8549 | Link (http://www.newark.com/on-semiconductor/mbr0520lt1g/rectifier-diode-single-20-v-500/dp/94W8549) |  |  | $0.09 | $1.74 | 463-432 | Link (http://it.rs-online.com/web/p/diodi-rettificatori-e-schottky/0463432/)
C9,C13,C15,C18,C22,C24,C31,C40 | 100nF |  | IPC7351-Nominal:CAPC1608X55 | Murata Electronics North America | GRM188R71E104KA01D | 80 | $0.02 | $1.53 | 9708975 |  | $0.09 | $6.88 | 490-1524-1-ND | Link (http://www.digikey.com/product-detail/en/murata-electronics-north-america/GRM188R71E104KA01D/490-1524-1-ND/587865) |  |  |  |  | 1828899 | Link (http://it.farnell.com/murata/grm188r71e104ka01d/condensatore-mlcc-x7r-100nf-25v/dp/1828899) | 16365 |  | $0.04 | $3.28 | 81-GRM39X104K25 | Link (http://www.mouser.com/Search/Refine.aspx?Keyword=GRM188R71E104KA01D%20) |  |  |  |  | 14T3317 | Link (http://www.newark.com/murata/grm188r71e104ka01d/capacitor-ceramic-0-1uf-10-25v/dp/14T3317) |  |  | $0.02 | $1.53 | 723-5638 | Link (http://it.rs-online.com/web/c/?searchTerm=GRM188R71E104KA01D%20)
T1,T2 | TRANS-2CT |  | manuf:WURTH-760390014 | Wurth Electronics Midcom | 760390014 | 20 | $1.71 | $34.20 | 22005 |  | $1.71 | $34.20 | 732-4458-1-ND | Link (http://www.digikey.com/product-detail/en/wurth-electronics-midcom/760390014/732-4458-1-ND/3831278) |  |  |  |  |  |  | 12153 |  | $2.02 | $40.40 | 710-760390014 | Link (http://www.mouser.com/Search/Refine.aspx?Keyword=760390014%20Wurth%20Electronics%20Midcom)
J8-J10 | current sensor |  | w_conn_jst-ph:b4b-ph-kl | JST Sales America Inc. | B4B-PH-K-S(LF)(SN) | 30 | $0.14 | $4.27 | 77385 |  | $0.23 | $6.81 | 455-1706-ND | Link (http://www.digikey.com/scripts/DkSearch/dksus.dll?WT.z_header=search_go&lang=en) |  |  | $0.14 | $4.27 | 9492437 | Link (http://it.farnell.com/webapp/wcs/stores/servlet/Search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) |  |  |  |  | Not Assigned | Link (http://www.mouser.com/ProductDetail/JST-Automotive/B4B-PH-K-S-LFSNP/) |  |  | $0.20 | $6.03 | 37K9958 | Link (http://www.newark.com/webapp/wcs/stores/servlet/Search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) | 740 |  | $0.17 | $4.97 | 820-1434 | Link (http://it.rs-online.com/web/p/file-di-contatti-da-pcb/8201434/)
R1,R3,R6,R8,R11,R13,R16,R18,R21-R24 | 500k |  | IPC7351-Nominal:RESC3216X60 | Yageo | AC1206FR-071ML | 120 | $0.02 | $2.16 | 4081 |  | $0.02 | $2.96 | YAG3832CT-ND | Link (http://www.digikey.com/product-detail/en/yageo/AC1206FR-071ML/YAG3832CT-ND/6006681) |  |  |  |  |  |  | 11380 |  | $0.02 | $2.16 | 603-AC1206FR-071ML | Link (http://www.mouser.com/Search/Refine.aspx?Keyword=AC1206FR-071ML%20Yageo) |  |  |  |  |  |  | 5 |  | $21.76 | $2611.15 | 618-0708 | Link (http://it.rs-online.com/web/c/?searchTerm=AC1206FR-071ML%20)
R4,R5,R9,R10,R14,R15,R19,R20 | 1k |  | IPC7351-Nominal:RESC1608X50 | Yageo | RC0603FR-071KL | 80 | $0.01 | $0.65 | 12991051 |  | $0.01 | $1.20 | 311-1.00KHRCT-ND | Link (http://www.digikey.com/product-detail/en/yageo/RC0603FR-071KL/311-1.00KHRCT-ND/729790) |  |  | $0.01 | $0.65 | 9238484 | Link (http://it.farnell.com/yageo-phycomp/rc0603fr-071kl/res-film-spesso-1k-1-0-1w-0603/dp/9238484) | 3078901 |  | $0.01 | $0.72 | 603-RC0603FR-071KL | Link (http://www.mouser.com/Search/Refine.aspx?Keyword=RC0603FR-071KL%20Yageo) |  |  | $0.01 | $0.80 | 68R0042 | Link (http://www.newark.com/yageo/rc0603fr-071kl/res-thick-film-1k-1-0-1w-0603/dp/68R0042)
U1 | LM1117IMP-v.v |  | smd-semi:SOT-223 | ON Semiconductor | NCV1117ST50T3G | 10 | $0.65 | $6.52 | 3864 |  | $0.78 | $7.82 | NCV1117ST50T3GOSCT-ND | Link (http://www.digikey.com/product-detail/en/on-semiconductor/NCV1117ST50T3G/NCV1117ST50T3GOSCT-ND/1967231) |  |  | $1.03 | $10.33 | 2534280 | Link (http://it.farnell.com/on-semiconductor/ncv1117st50t3g/ldo-fissa-5v-1a-sot-223-3/dp/2534280) | 2810 |  | $0.71 | $7.15 | 863-NCV1117ST50T3G | Link (http://www.mouser.com/Search/Refine.aspx?Keyword=NCV1117ST50T3G%20) |  |  | $0.82 | $8.21 | 81Y6964 | Link (http://www.newark.com/webapp/wcs/stores/servlet/Search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) | 240 |  | $0.65 | $6.52 | 802-1743 | Link (http://it.rs-online.com/web/c/?searchTerm=NCV1117ST50T3G%20)
J5 | CONN-100MIL-F-1x2 |  | w_conn_screw:mstba_2,5%2f2-g-5,08 | Phoenix Contact | 1923869 | 10 | $0.53 | $5.25 | 565 |  | $0.69 | $6.85 | 277-6570-ND | Link (http://www.digikey.com/scripts/DkSearch/dksus.dll?WT.z_header=search_go&lang=en&keywords=1923869%20) |  |  | $0.53 | $5.25 | 2776387 | Link (http://it.farnell.com/webapp/wcs/stores/servlet/Search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) | 100 |  | $0.69 | $6.87 | 651-1923869 | Link (http://www.mouser.com/Search/Refine.aspx?Keyword=1923869%20) |  |  | $0.67 | $6.73 | 32AC7953 | Link (http://www.newark.com/webapp/wcs/stores/servlet/Search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) |  |  |  |  | 859-8303 | Link (http://it.rs-online.com/web/p/file-di-contatti-da-pcb/8598303/)
C8,C14,C17,C23,C32,C41 | 2.2uF |  | IPC7351-Nominal:CAPC1608X55 | Murata Electronics North America | GRM188R71A225KE15D | 60 | $0.13 | $7.65 | 1297812 |  | $0.20 | $11.94 | 490-4520-1-ND | Link (http://www.digikey.com/product-detail/en/murata-electronics-north-america/GRM188R71A225KE15D/490-4520-1-ND/1033279) |  |  | $0.13 | $7.65 | 1797012 | Link (http://it.farnell.com/murata/grm188r71a225ke15d/condensatore-mlcc-x7r-2-2uf-10v/dp/1797012) |  |  | $0.22 | $13.14 | 81-GRM188R71A225KE15 | Link (http://www.mouser.com/Search/Refine.aspx?Keyword=GRM188R71A225KE15D%20) |  |  | $0.15 | $8.88 | 72R4209 | Link (http://www.newark.com/murata/grm188r71a225ke15d/ceramic-capacitor-2-2uf-10v-x7r/dp/72R4209) | 900 |  | $0.13 | $7.97 | 723-5597 | Link (http://it.rs-online.com/web/c/?searchTerm=GRM188R71A225KE15D%20)
C1,C4,C10,C16,C19,C25 | 22uF |  | IPC7351-Nominal:CAPC2012X70 | TDK Corporation | C2012X5R1V226M125AC | 60 | $0.60 | $36.23 | 136916 |  | $0.86 | $51.78 | 445-14428-1-ND | Link (http://www.digikey.com/product-detail/en/tdk-corporation/C2012X5R1V226M125AC/445-14428-1-ND/3956094) |  |  | $0.60 | $36.23 | 2528773 | Link (http://it.farnell.com/tdk/c2012x5r1v226m125ac/condensatore-mlcc-x5r-22uf-35v/dp/2528773) |  |  | $1.10 | $66.00 | 810-C2012X5R1V226MAC | Link (http://www.mouser.com/Search/Refine.aspx?Keyword=C2012X5R1V226M125AC%20) |  |  | $0.76 | $45.36 | 78Y9944 | Link (http://www.newark.com/webapp/wcs/stores/servlet/Search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) |  |  | $0.81 | $48.86 | 915-9334 | Link (http://it.rs-online.com/web/p/condensatori-ceramici-multistrato/9159334/)
C2,C3,C5-C7 | 100nF |  | IPC7351-Nominal:CAPC1608X55 | Murata Electronics North America | GRM188R71E104KA01D | 50 | $0.02 | $0.96 | 9708975 |  | $0.09 | $4.30 | 490-1524-1-ND | Link (http://www.digikey.com/product-detail/en/murata-electronics-north-america/GRM188R71E104KA01D/490-1524-1-ND/587865) |  |  |  |  | 1828899 | Link (http://it.farnell.com/murata/grm188r71e104ka01d/condensatore-mlcc-x7r-100nf-25v/dp/1828899) |  |  |  |  |  |  |  |  |  |  | 14T3317 | Link (http://www.newark.com/murata/grm188r71e104ka01d/capacitor-ceramic-0-1uf-10-25v/dp/14T3317) |  |  | $0.02 | $0.96 | 723-5638 | Link (http://it.rs-online.com/web/c/?searchTerm=GRM188R71E104KA01D%20)
J2 | GATE_DRIVER_CONN_V |  | conn-100mil:CONN-100MIL-M-2x8 | Amphenol FCI | 87606-308LF | 10 | $1.77 | $17.70 | 1177 |  | $1.97 | $19.65 | 609-3554-ND | Link (http://www.digikey.com/scripts/DkSearch/dksus.dll?WT.z_header=search_go&lang=en) |  |  | $2.00 | $19.98 | 1278235 | Link (http://it.farnell.com/webapp/wcs/stores/servlet/Search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) | 346 |  | $1.77 | $17.70 | 649-87606-308LF | Link (http://www.mouser.com/Search/Refine.aspx?Keyword=87606-308LF%20) |  |  | $1.92 | $19.20 | 63K0748 | Link (http://www.newark.com/webapp/wcs/stores/servlet/Search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) |  |  | $1.83 | $18.29 | 859-9488 | Link (http://it.rs-online.com/web/c/?searchTerm=87606-308LF%20)
C12,C21,C30,C39 | 330pF |  | IPC7351-Nominal:CAPC1608X55 | Murata Electronics North America | GCM1885C1H331JA16D | 40 | $0.03 | $1.02 | 63781 |  | $0.09 | $3.76 | 490-4964-1-ND | Link (http://www.digikey.com/product-detail/en/murata-electronics-north-america/GCM1885C1H331JA16D/490-4964-1-ND/1765283) |  |  | $0.03 | $1.05 | 2688476 | Link (http://it.farnell.com/murata/gcm1885c1h331ja16d/cond-mlcc-c0g-330pf-50v-0603/dp/2688476) |  |  |  |  |  |  |  |  | $0.05 | $1.84 | 06AC6012 | Link (http://www.newark.com/webapp/wcs/stores/servlet/Search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) | 1400 |  | $0.03 | $1.02 | 815-1314 | Link (http://it.rs-online.com/web/c/?searchTerm=GCM1885C1H331JA16D%20)
J1 | GATE_DRIVER_CONN_U |  | conn-100mil:CONN-100MIL-M-2x8 | Amphenol FCI | 87606-308LF | 10 | $1.77 | $17.70 | 1177 |  | $1.97 | $19.65 | 609-3554-ND | Link (http://www.digikey.com/scripts/DkSearch/dksus.dll?WT.z_header=search_go&lang=en) |  |  | $2.00 | $19.98 | 1278235 | Link (http://it.farnell.com/webapp/wcs/stores/servlet/Search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) | 346 |  | $1.77 | $17.70 | 649-87606-308LF | Link (http://www.mouser.com/Search/Refine.aspx?Keyword=87606-308LF%20) |  |  | $1.92 | $19.20 | 63K0748 | Link (http://www.newark.com/webapp/wcs/stores/servlet/Search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) |  |  | $1.83 | $18.29 | 859-9488 | Link (http://it.rs-online.com/web/c/?searchTerm=87606-308LF%20)
U2,U5 | SN6501DBV |  | smd-semi:SOT-23-5 | Texas Instruments | SN6501DBVR | 20 | $1.10 | $22.00 | 36553 |  | $1.97 | $39.30 | 296-37700-1-ND | Link (http://www.digikey.com/product-detail/en/texas-instruments/SN6501DBVR/296-37700-1-ND/4833928) |  |  | $1.17 | $23.39 | 2542737 | Link (http://it.farnell.com/webapp/wcs/stores/servlet/Search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) |  |  |  |  |  |  |  |  | $1.10 | $22.00 | 81Y9761 | Link (http://www.newark.com/webapp/wcs/stores/servlet/Search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)
Q1 | NMOS |  |  |  |  | 10 | $0.00 | $0.00
M1-M3 | Current sensor part# |  |  |  | ISB-425-A-800 | 30 | $21.55 | $646.50 |  |  |  |  |  |  |  |  |  |  |  |  | 15 |  | $21.55 | $646.50 | 911-ISB-425-A-800 | Link (http://www.mouser.com/Search/Refine.aspx?Keyword=ISB-425-A-800%20)

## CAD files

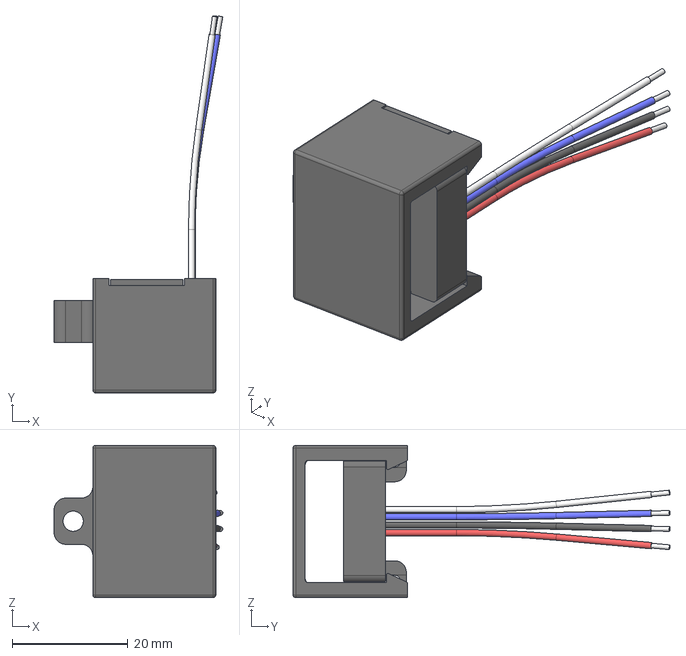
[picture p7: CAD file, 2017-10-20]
adaptor boards/power_integrations_2SP0115T2A/mechanical/ISB_Wired.stp
29.2 x 65.3 x 26.4 mm

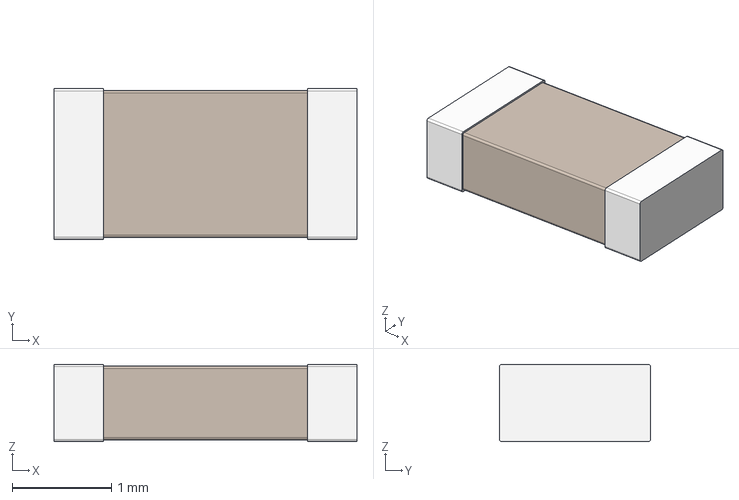
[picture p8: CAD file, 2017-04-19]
pcb_design/3Dlib/c_1206_h078.step
3.05 x 1.52 x 0.78 mm

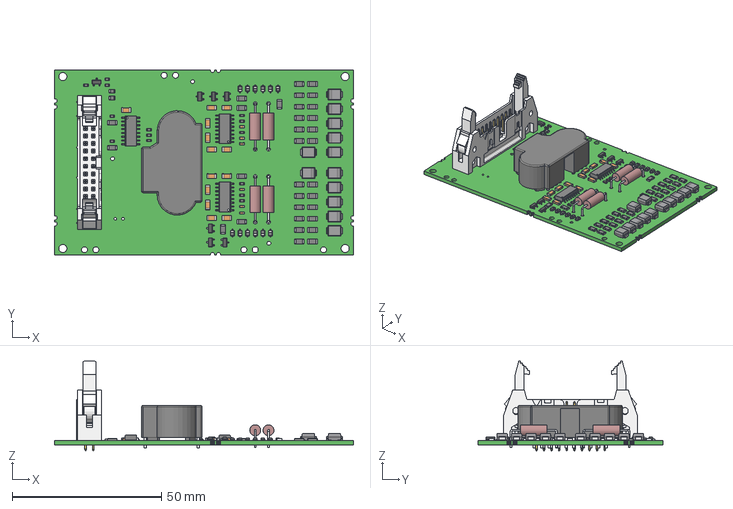
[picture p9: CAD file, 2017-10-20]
adaptor boards/power_integrations_2SP0115T2A/mechanical/2SP0115T2A0_3D_v3.stp
100.1 x 62.0 x 30.0 mm

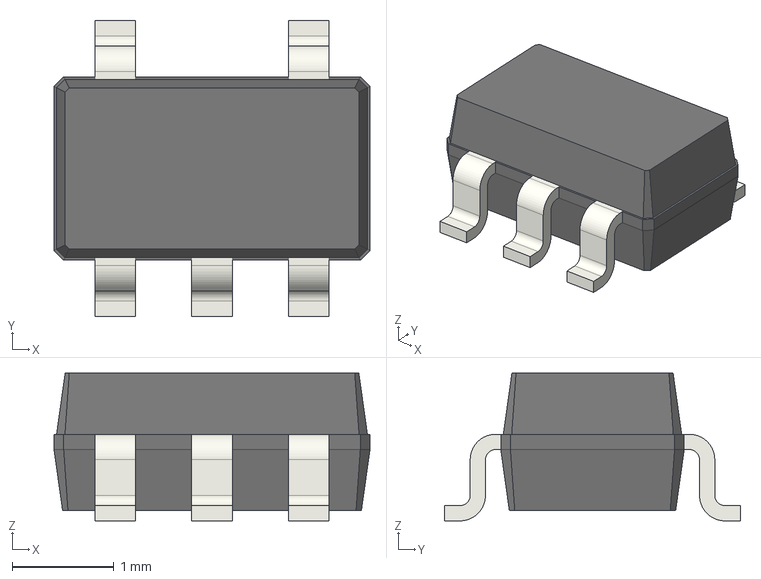
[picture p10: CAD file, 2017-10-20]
adaptor boards/power_integrations_2SP0115T2A/pcb_design/3Dlib/sot23_5_18x29_p095.step
3.10 x 2.90 x 1.45 mm

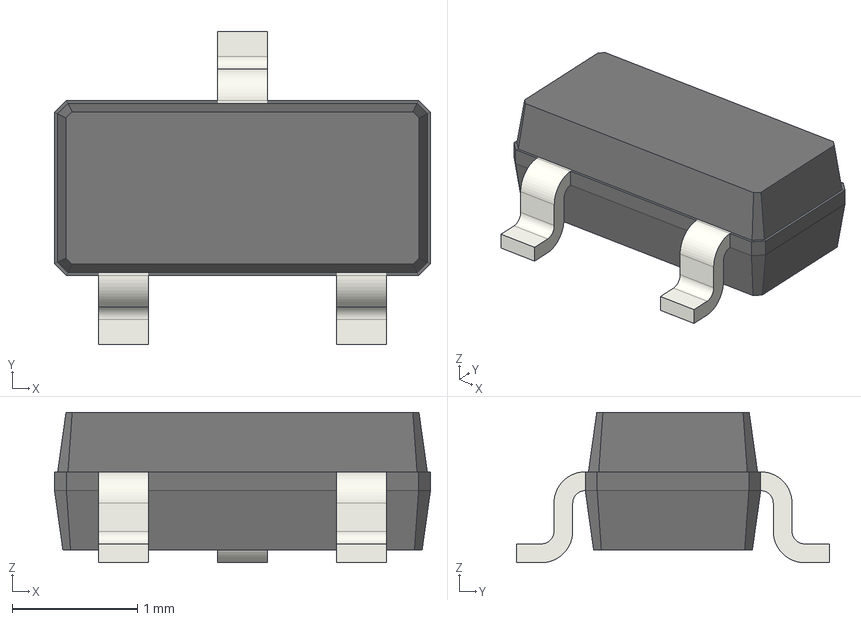
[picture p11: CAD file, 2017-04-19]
pcb_design/3Dlib/sot23_3_25x30_p095.step
3.00 x 2.50 x 1.20 mm

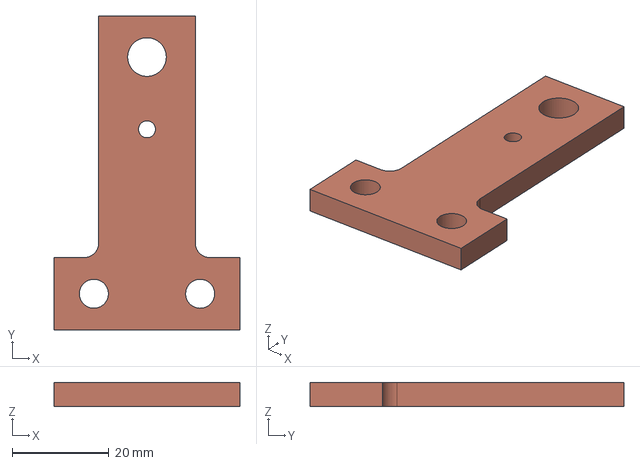
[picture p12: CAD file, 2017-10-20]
adaptor boards/power_integrations_2SP0115T2A/mechanical/phase_busbar.step
38.5 x 65.0 x 5.00 mm

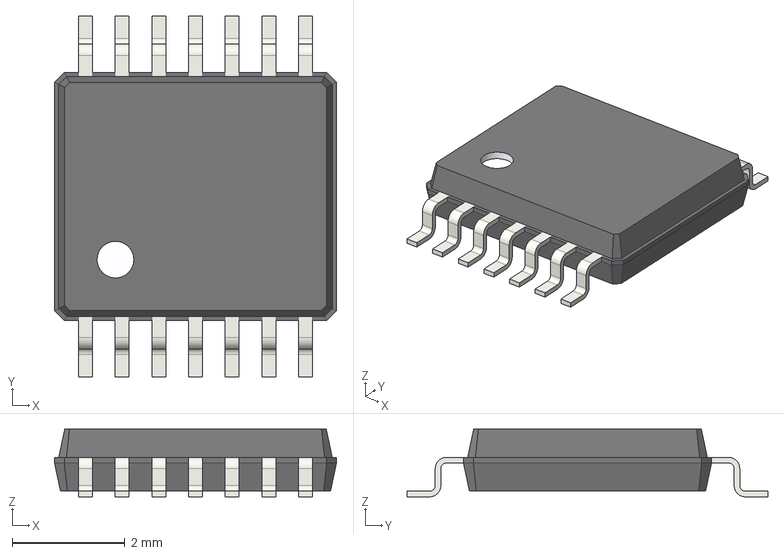
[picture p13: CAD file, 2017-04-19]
pcb_design/3Dlib/tssop_14_50x44_p065.step
5.00 x 6.40 x 1.20 mm

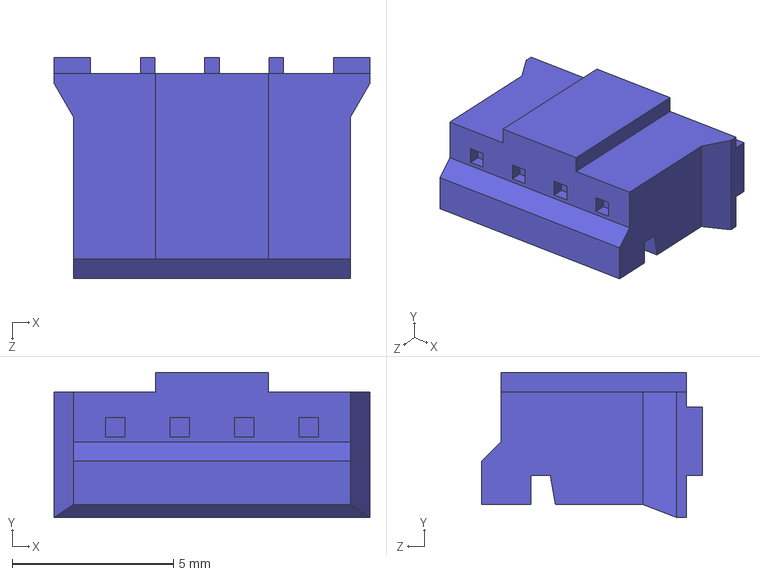
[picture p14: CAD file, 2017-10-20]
adaptor boards/power_integrations_2SP0115T2A/mechanical/PHR-4.STEP
9.80 x 4.50 x 6.85 mm

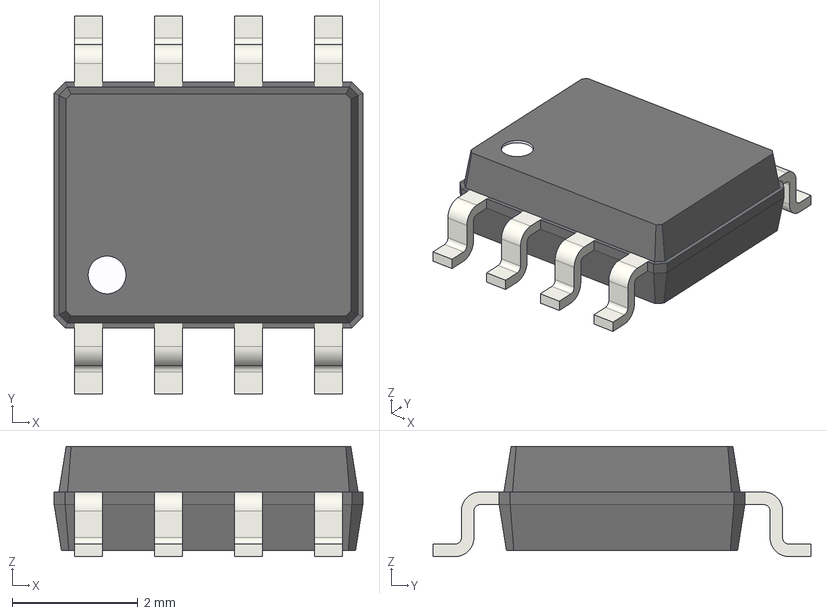
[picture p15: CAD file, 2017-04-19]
pcb_design/3Dlib/soic_8_39x49_p127.step
4.90 x 6.00 x 1.75 mm

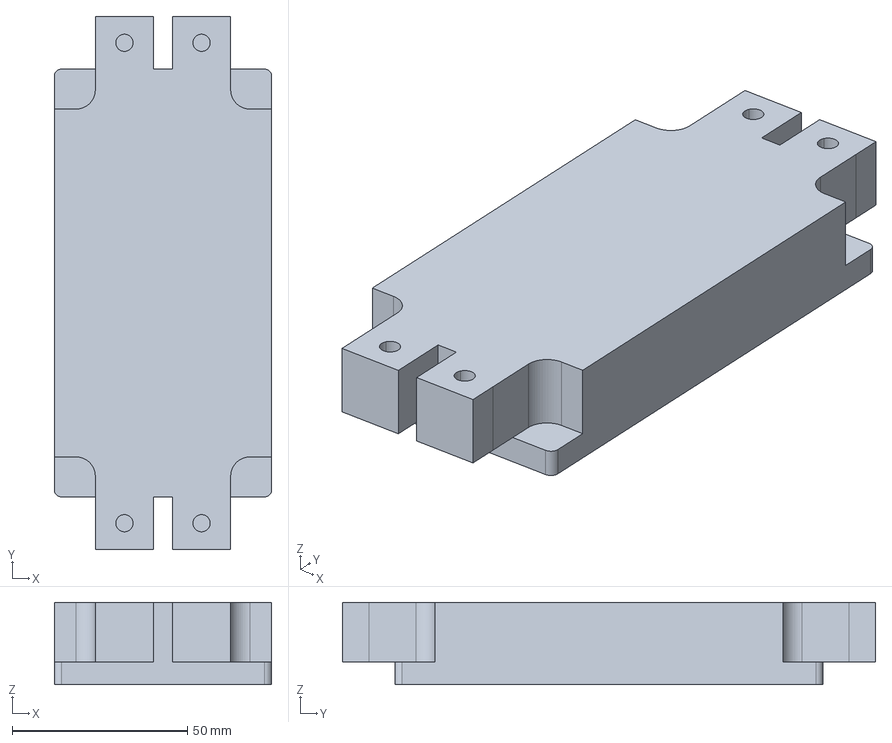
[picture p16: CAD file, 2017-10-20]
adaptor boards/power_integrations_2SP0115T2A/mechanical/INFINEON_FF600R06ME3.stp
62.0 x 152.0 x 23.5 mm

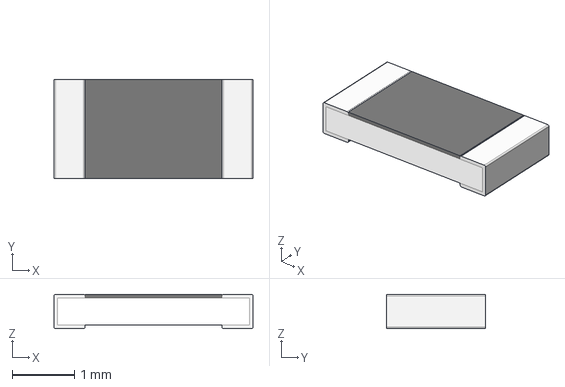
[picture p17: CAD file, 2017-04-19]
adaptor boards/power_integrations_2SP0115T2A/pcb_design/3Dlib/r_1206_h055.step
3.20 x 1.60 x 0.55 mm

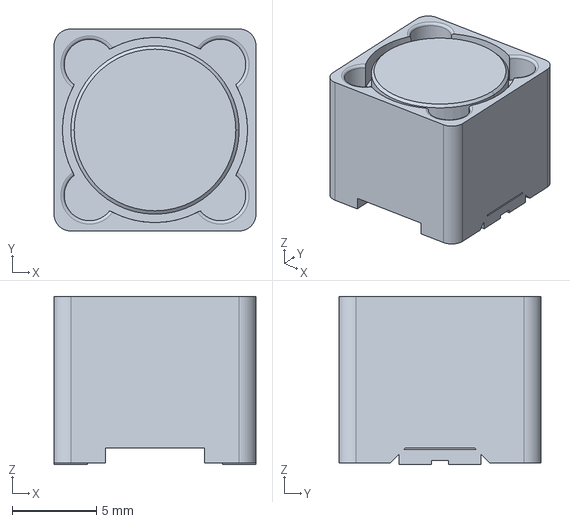
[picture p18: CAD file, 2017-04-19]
pcb_design/3Dlib/srr1210.step
12.0 x 12.0 x 10.0 mm

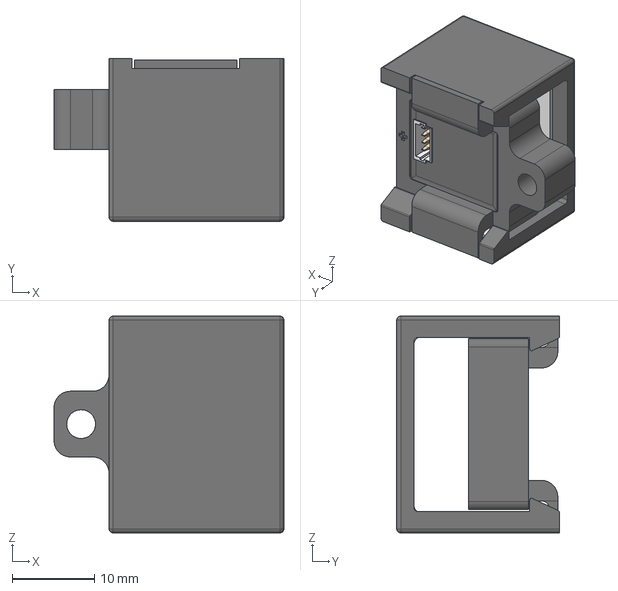
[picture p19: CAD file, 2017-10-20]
adaptor boards/power_integrations_2SP0115T2A/mechanical/ISB_Connector.stp
28.0 x 19.8 x 26.4 mm

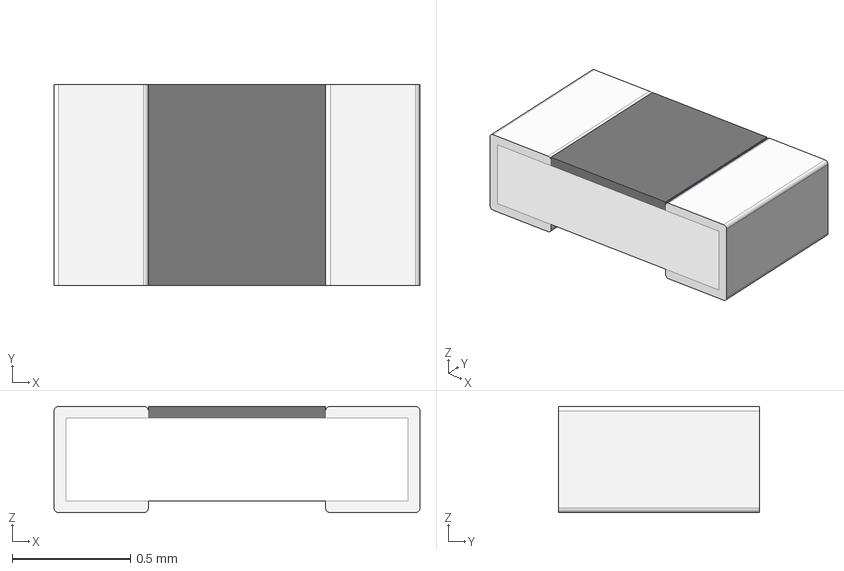
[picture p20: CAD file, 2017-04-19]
adaptor boards/power_integrations_2SP0115T2A/pcb_design/3Dlib/r_0603_h078.step
1.55 x 0.85 x 0.45 mm

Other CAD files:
pcb_design/3Dlib/r_0805_h078.step
adaptor boards/power_integrations_2SP0115T2A/pcb_design/3Dlib/c_0603_h078.step
pcb_design/3Dlib/tssop_8_23x20_p050.step
adaptor boards/power_integrations_2SP0115T2A/pcb_design/3Dlib/c_0805_h078.step
adaptor boards/power_integrations_2SP0115T2A/pcb_design/3Dlib/1757268_06.step
adaptor boards/power_integrations_2SP0115T2A/pcb_design/3Dlib/1923869_02.step
adaptor boards/power_integrations_2SP0115T2A/pcb_design/3Dlib/1923872_02.step
adaptor boards/power_integrations_2SP0115T2A/pcb_design/3Dlib/250-1109-rev1.step
adaptor boards/power_integrations_2SP0115T2A/pcb_design/3Dlib/75869104LF.step
adaptor boards/power_integrations_2SP0115T2A/pcb_design/3Dlib/B4B-PH-K-S.step
adaptor boards/power_integrations_2SP0115T2A/pcb_design/3Dlib/soic_8_75x58_p127.step
pcb_design/3Dlib/ABM3B.step
pcb_design/3Dlib/B3U_1000P.step
pcb_design/3Dlib/Tantalum_D_7343H31.step
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

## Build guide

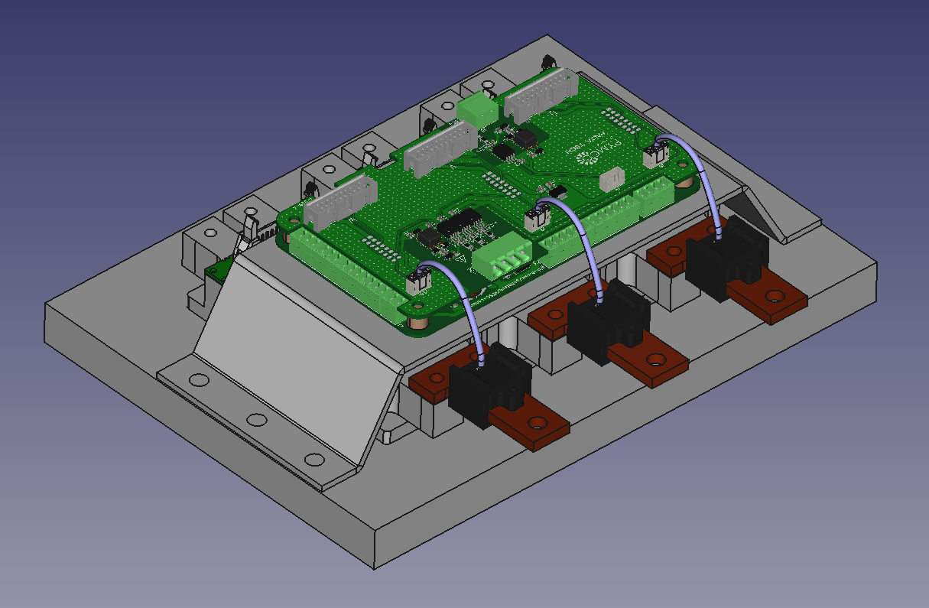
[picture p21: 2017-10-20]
adaptor boards/power_integrations_2SP0115T2A/doc/assembly.png

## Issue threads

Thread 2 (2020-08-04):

JLCPCB BOM&CPL files

rusefillc, 2020-08-04:
with many components on one side it could simplify assembly if boards come with JLC BOM&CPL files - JLC would cheaply assemble a significant percentage of the board

rusefillc, 2020-08-04:
@jharvey FYI

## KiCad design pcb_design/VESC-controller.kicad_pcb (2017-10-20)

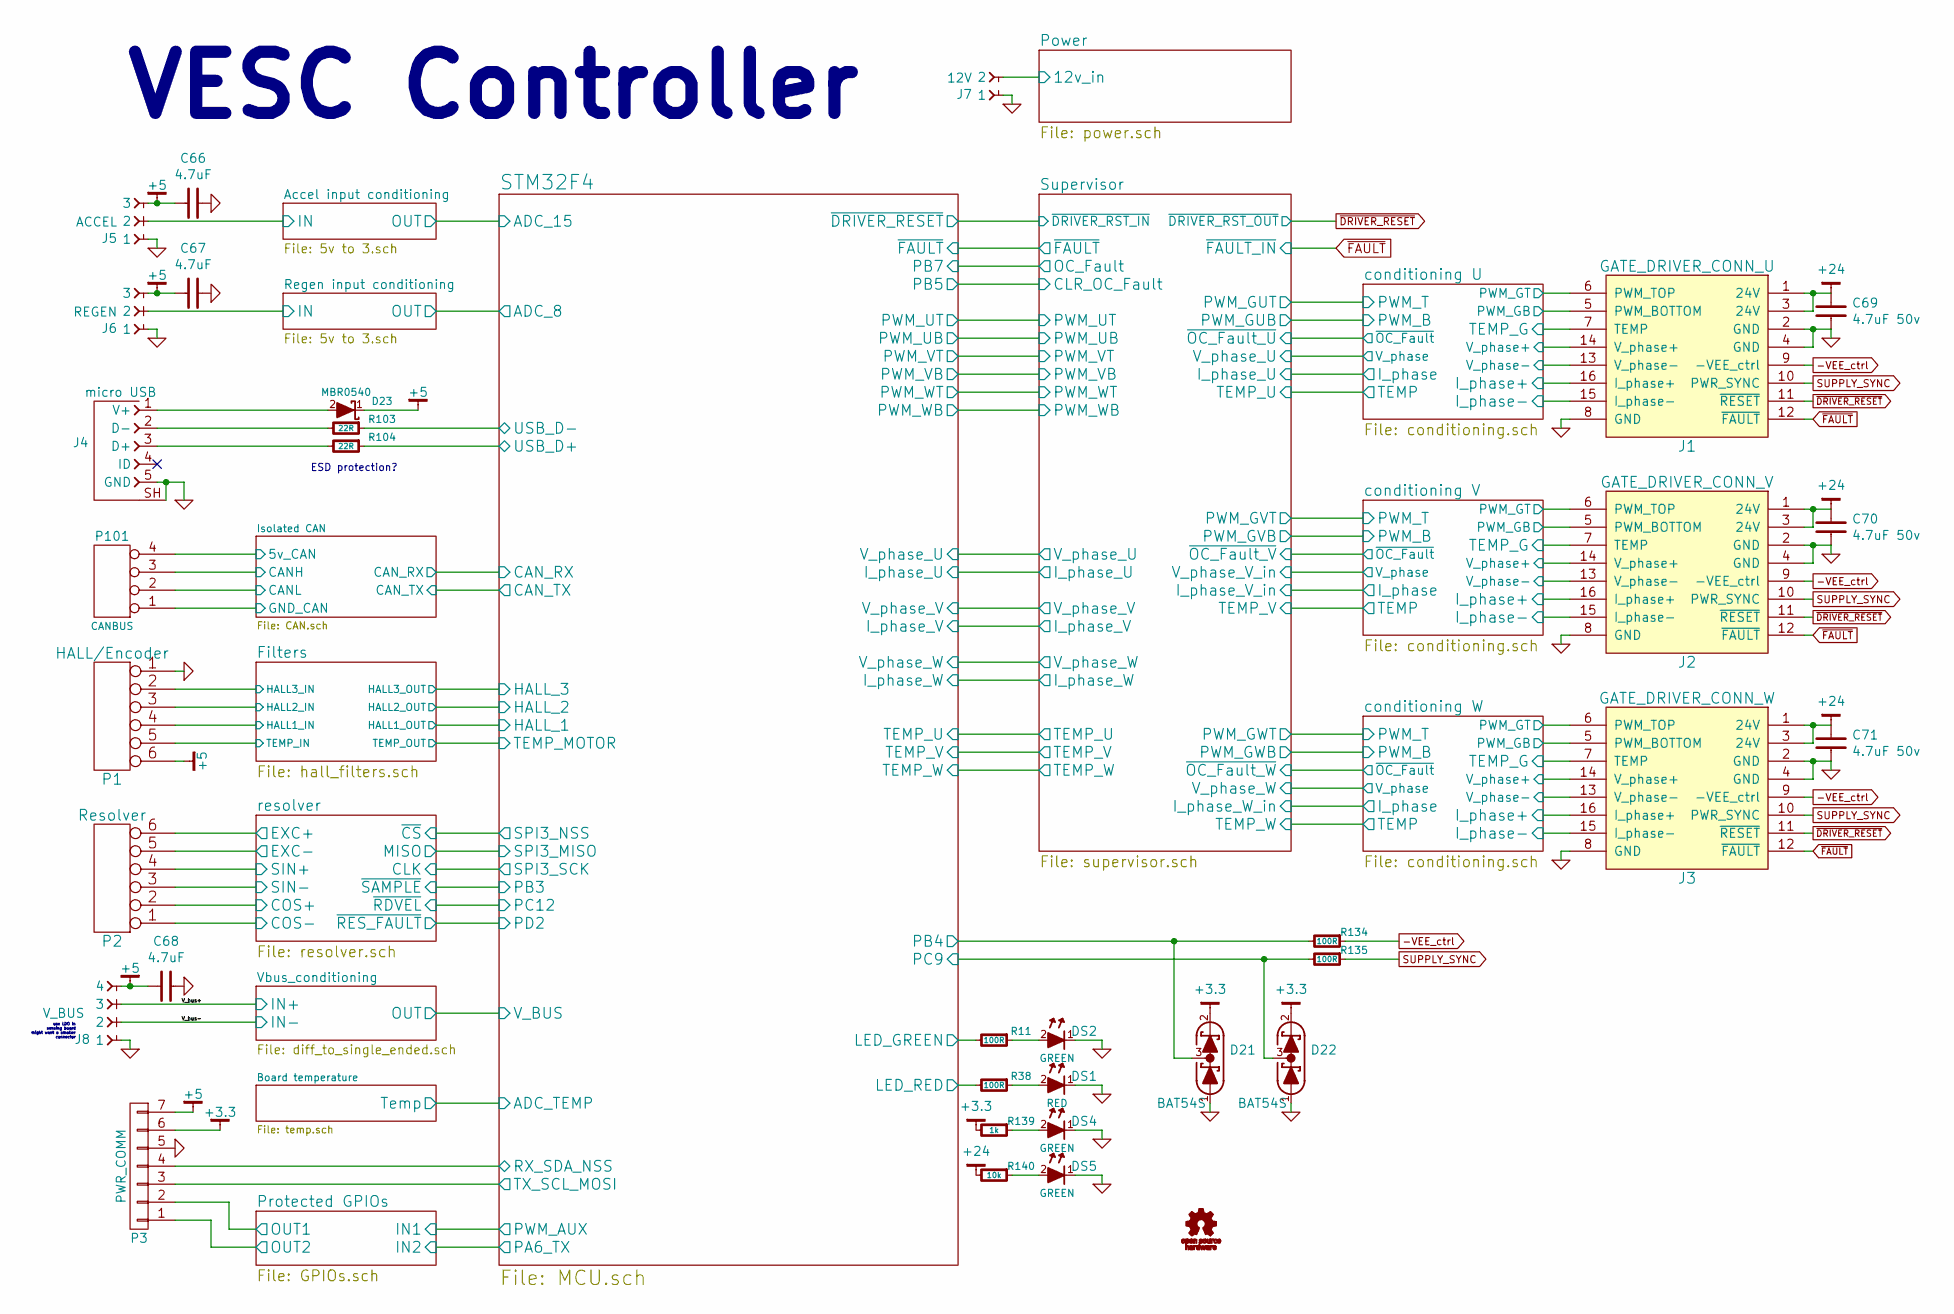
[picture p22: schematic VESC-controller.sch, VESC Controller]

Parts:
C66, C67, C68: 4.7uF; CAPC2012X70; MPN GRM21BR71A475KA73K
C69, C70, C71: 4.7uF 50v; CAPC3216X70; MPN GRM31CR71H475KA12L
D21, D22: BAT54S; SOT-23; mfg# TBAT54S,LM
D23: MBR0540; SOD-123; MPN MBR0540
DS1: RED; LED-0603; MPN LTST-C191KRKT
DS2, DS4, DS5: GREEN; LED-0603; MPN LTST-C191KGKT
J1: GATE_DRIVER_CONN_U; CONN-100MIL-M-2x8; MPN 67997-216HLF
J2: GATE_DRIVER_CONN_V; CONN-100MIL-M-2x8; MPN 67997-216HLF
J3: GATE_DRIVER_CONN_W; CONN-100MIL-M-2x8; MPN 67997-216HLF
J4: micro USB; CONN-10118194-0001LF-FCI; mfg# 10118194-0001LF
J5: ACCEL; mcv_1,5-3-G-3,81; MPN 1803439
J6: REGEN; mcv_1,5-3-G-3,81; MPN 1803439
J7: 12V; mcv_1,5-2-G-3,81; MPN 1803426
J8: V_BUS; mcv_1,5-4-G-3,81; MPN 1803442
P1: HALL/Encoder; mcv_1,5-6-G-3,81; MPN 1803468
P2: Resolver; mcv_1,5-6-G-3,81; MPN 1803468
P3: PWR_COMM; mcv_1,5-7-G-3,81; MPN 1803471
P101: CANBUS; b4b-ph-kl; MPN B4B-PH-K-S(LF)(SN)
R11, R38, R134, R135: 100R; RESC1608X50; MPN RC0603FR-07100RL
R103, R104: 22R; RESC1608X50; MPN RC0603FR-0722RL
R139: 1k; RESC1608X50; MPN RC0603FR-071KL
R140: 10k; RESC1608X50; MPN RC0603FR-0710KL

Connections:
+3.3: D21.2 (K), D22.2 (K), P3.6, R139.2; also elsewhere on the board
-VEE_ctrl: J1.9 (-VEE_ctrl), J2.9 (-VEE_ctrl), J3.9 (-VEE_ctrl), R134.1
/Accel input conditioning/IN: J5.2; also elsewhere on the board
/Filters/HALL1_IN: P1.4; also elsewhere on the board
/Filters/HALL2_IN: P1.3; also elsewhere on the board
/Filters/HALL3_IN: P1.2; also elsewhere on the board
/Filters/TEMP_IN: P1.5; also elsewhere on the board
/Isolated CAN/5v_CAN: P101.4; also elsewhere on the board
/Isolated CAN/CANH: P101.3; also elsewhere on the board
/Isolated CAN/CANL: P101.2; also elsewhere on the board
/Isolated CAN/GND_CAN: P101.1; also elsewhere on the board
/Power/12v_in: J7.2; also elsewhere on the board
/Protected GPIOs/OUT1: P3.2; also elsewhere on the board
/Protected GPIOs/OUT2: P3.1; also elsewhere on the board
/Regen input conditioning/IN: J6.2; also elsewhere on the board
/STM32F4/LED_GREEN: R11.2; also elsewhere on the board
/STM32F4/LED_RED: R38.2; also elsewhere on the board
/STM32F4/PB4: D21.3 (COM), R134.2; also elsewhere on the board
/STM32F4/PC9: D22.3 (COM), R135.2; also elsewhere on the board
/STM32F4/RX_SDA_NSS: P3.4; also elsewhere on the board
/STM32F4/TX_SCL_MOSI: P3.3; also elsewhere on the board
/STM32F4/USB_D+: R104.1; also elsewhere on the board
/STM32F4/USB_D-: R103.1; also elsewhere on the board
/V_bus+: J8.3; also elsewhere on the board
/V_bus-: J8.2; also elsewhere on the board
/conditioning U/I_phase+: J1.16 (I_phase+); also elsewhere on the board
/conditioning U/I_phase-: J1.15 (I_phase-); also elsewhere on the board
/conditioning U/PWM_GB: J1.5 (PWM_BOTTOM); also elsewhere on the board
/conditioning U/PWM_GT: J1.6 (PWM_TOP); also elsewhere on the board
/conditioning U/TEMP_G: J1.7 (TEMP); also elsewhere on the board
/conditioning U/V_phase+: J1.14 (V_phase+); also elsewhere on the board
/conditioning U/V_phase-: J1.13 (V_phase-); also elsewhere on the board
/conditioning V/I_phase+: J2.16 (I_phase+); also elsewhere on the board
/conditioning V/I_phase-: J2.15 (I_phase-); also elsewhere on the board
/conditioning V/PWM_GB: J2.5 (PWM_BOTTOM); also elsewhere on the board
/conditioning V/PWM_GT: J2.6 (PWM_TOP); also elsewhere on the board
/conditioning V/TEMP_G: J2.7 (TEMP); also elsewhere on the board
/conditioning V/V_phase+: J2.14 (V_phase+); also elsewhere on the board
/conditioning V/V_phase-: J2.13 (V_phase-); also elsewhere on the board
/conditioning W/I_phase+: J3.16 (I_phase+); also elsewhere on the board
/conditioning W/I_phase-: J3.15 (I_phase-); also elsewhere on the board
/conditioning W/PWM_GB: J3.5 (PWM_BOTTOM); also elsewhere on the board
/conditioning W/PWM_GT: J3.6 (PWM_TOP); also elsewhere on the board
/conditioning W/TEMP_G: J3.7 (TEMP); also elsewhere on the board
/conditioning W/V_phase+: J3.14 (V_phase+); also elsewhere on the board
/conditioning W/V_phase-: J3.13 (V_phase-); also elsewhere on the board
/resolver/COS+: P2.2; also elsewhere on the board
/resolver/COS-: P2.1; also elsewhere on the board
/resolver/EXC+: P2.6; also elsewhere on the board
/resolver/EXC-: P2.5; also elsewhere on the board
/resolver/SIN+: P2.4; also elsewhere on the board
/resolver/SIN-: P2.3; also elsewhere on the board
unnamed: D23.2 (A), J4.1 (V+)
unnamed: DS1.2 (A), R38.1
unnamed: DS2.2 (A), R11.1
unnamed: DS4.2 (A), R139.1
unnamed: DS5.2 (A), R140.1
unnamed: J4.2 (D-), R103.2
unnamed: J4.3 (D+), R104.2
SUPPLY_SYNC: J1.10 (PWR_SYNC), J2.10 (PWR_SYNC), J3.10 (PWR_SYNC), R135.1
~DRIVER_RESET: J1.11 (~RESET), J2.11 (~RESET), J3.11 (~RESET); also elsewhere on the board
~FAULT: J1.12 (~FAULT), J2.12 (~FAULT), J3.12 (~FAULT); also elsewhere on the board

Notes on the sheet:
ESD protection?
VESC Controller
use LDO in sensing board might want a smaller connector

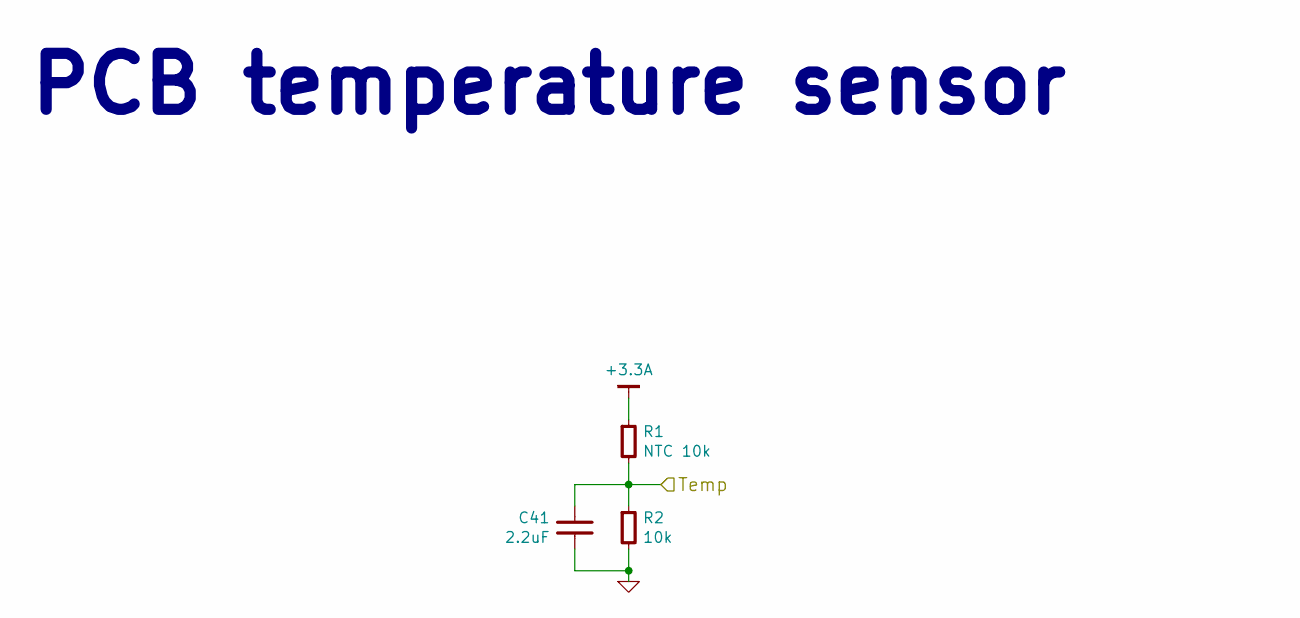
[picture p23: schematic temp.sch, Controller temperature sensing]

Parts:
C41: 2.2uF; CAPC1608X55; MPN GRM188R71A225KE15D
R1: NTC 10k; RESC1608X50; MPN NCP18XH103F03RB
R2: 10k; RESC1608X50; MPN RC0603FR-0710KL

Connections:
+3.3A: R1.1; also elsewhere on the board
/STM32F4/ADC_TEMP: C41.1, R1.2, R2.1; also elsewhere on the board

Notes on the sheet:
PCB temperature sensor

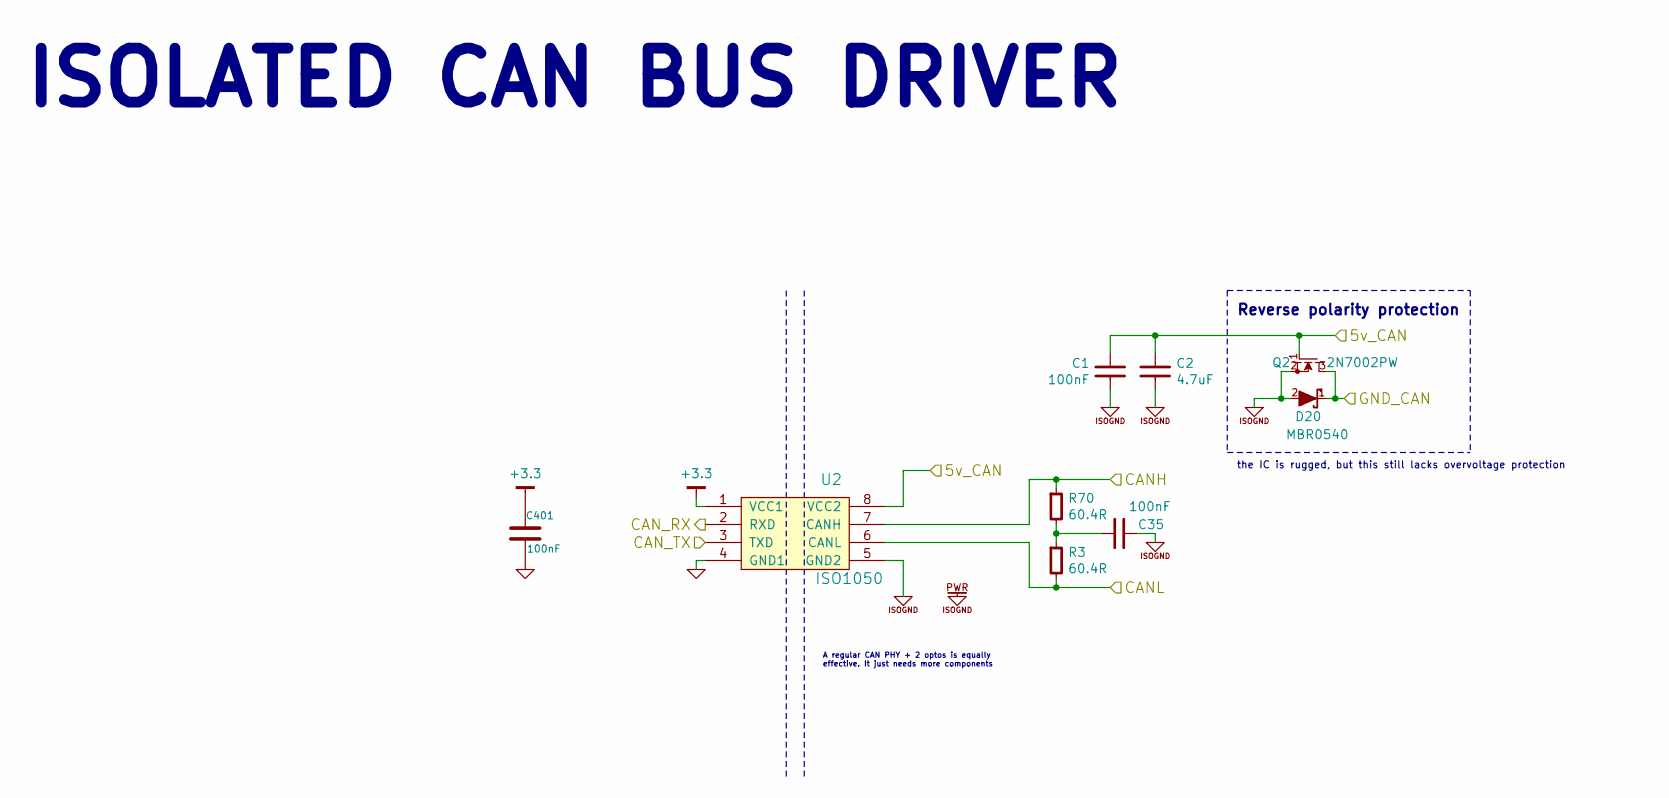
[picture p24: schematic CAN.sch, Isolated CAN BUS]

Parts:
C1, C35, C401: 100nF; CAPC1608X55; MPN GRM188R71E104KA01D
C2: 4.7uF; CAPC2012X70; MPN GRM21BR71A475KA73K
D20: MBR0540; SOD-123; MPN MBR0540
Q2: 2N7002PW; SC-70; mfg# 2N7002PW,115
R3, R70: 60.4R; RESC1608X50; MPN RC0603FR-0760R4L
U2: ISO1050; SO8-ISO1050; mfg# ISO1050DUBR

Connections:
+3.3: C401.1, U2.1 (VCC1); also elsewhere on the board
/Isolated CAN/5v_CAN: C1.1, C2.1, Q2.1 (G), U2.8 (VCC2); also elsewhere on the board
/Isolated CAN/CANH: R70.1, U2.7 (CANH); also elsewhere on the board
/Isolated CAN/CANL: R3.2, U2.6 (CANL); also elsewhere on the board
/Isolated CAN/CAN_RX: U2.2 (RXD); also elsewhere on the board
/Isolated CAN/CAN_TX: U2.3 (TXD); also elsewhere on the board
/Isolated CAN/GND_CAN: D20.1 (K), Q2.3 (D); also elsewhere on the board
ISOGND: C1.2, C2.2, C35.1, D20.2 (A), Q2.2 (S), U2.5 (GND2)
unnamed: C35.2, R3.1, R70.2

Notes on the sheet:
ISOLATED CAN BUS DRIVER
Reverse polarity protection
the IC is rugged, but this still lacks overvoltage protection
A regular CAN PHY + 2 optos is equally effective. It just needs more components

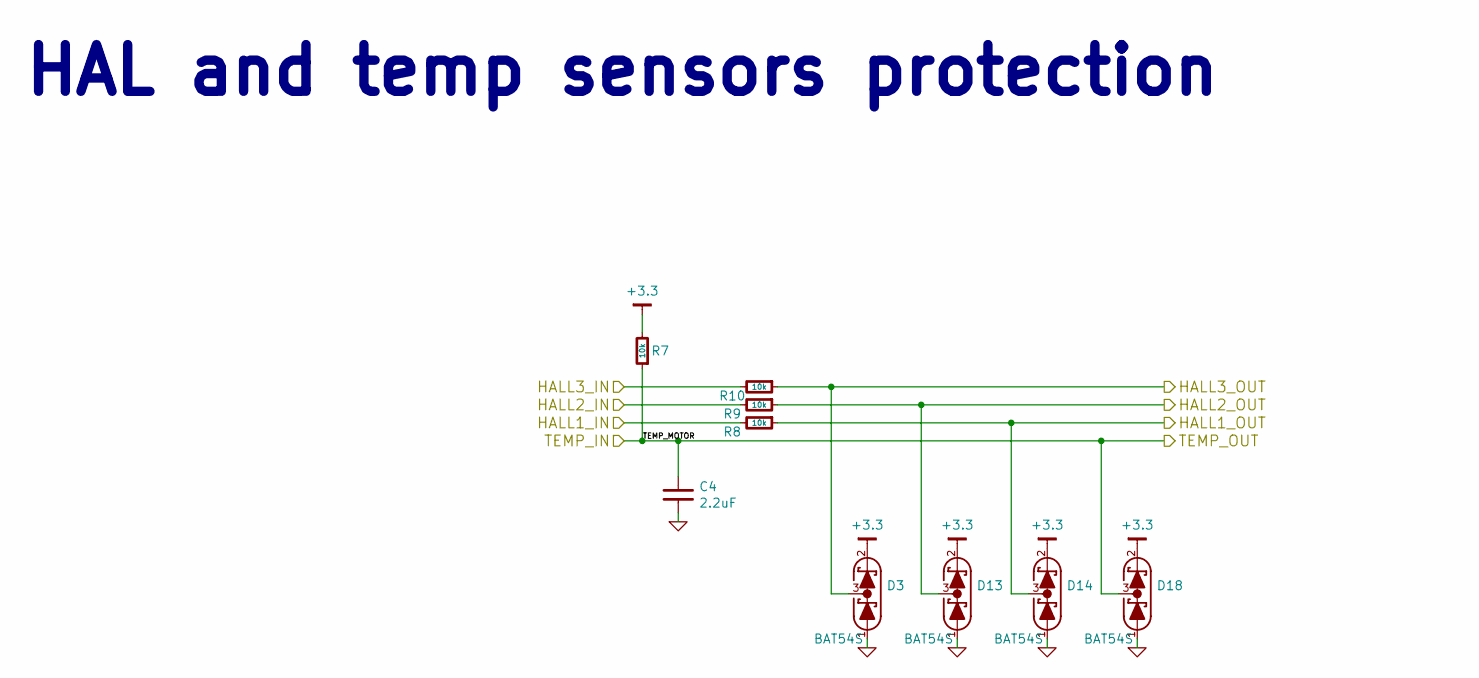
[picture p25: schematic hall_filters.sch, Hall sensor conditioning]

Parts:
C4: 2.2uF; CAPC1608X55; MPN GRM188R71A225KE15D
D3, D13, D14, D18: BAT54S; SOT-23; mfg# TBAT54S,LM
R7, R8, R9, R10: 10k; RESC1608X50; MPN RC0603FR-0710KL

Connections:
+3.3: D3.2 (K), D13.2 (K), D14.2 (K), D18.2 (K), R7.2; also elsewhere on the board
/Filters/HALL1_IN: R8.2; also elsewhere on the board
/Filters/HALL1_OUT: D14.3 (COM), R8.1; also elsewhere on the board
/Filters/HALL2_IN: R9.2; also elsewhere on the board
/Filters/HALL2_OUT: D13.3 (COM), R9.1; also elsewhere on the board
/Filters/HALL3_IN: R10.2; also elsewhere on the board
/Filters/HALL3_OUT: D3.3 (COM), R10.1; also elsewhere on the board
/Filters/TEMP_IN: C4.1, D18.3 (COM), R7.1; also elsewhere on the board

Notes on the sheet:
HAL and temp sensors protection

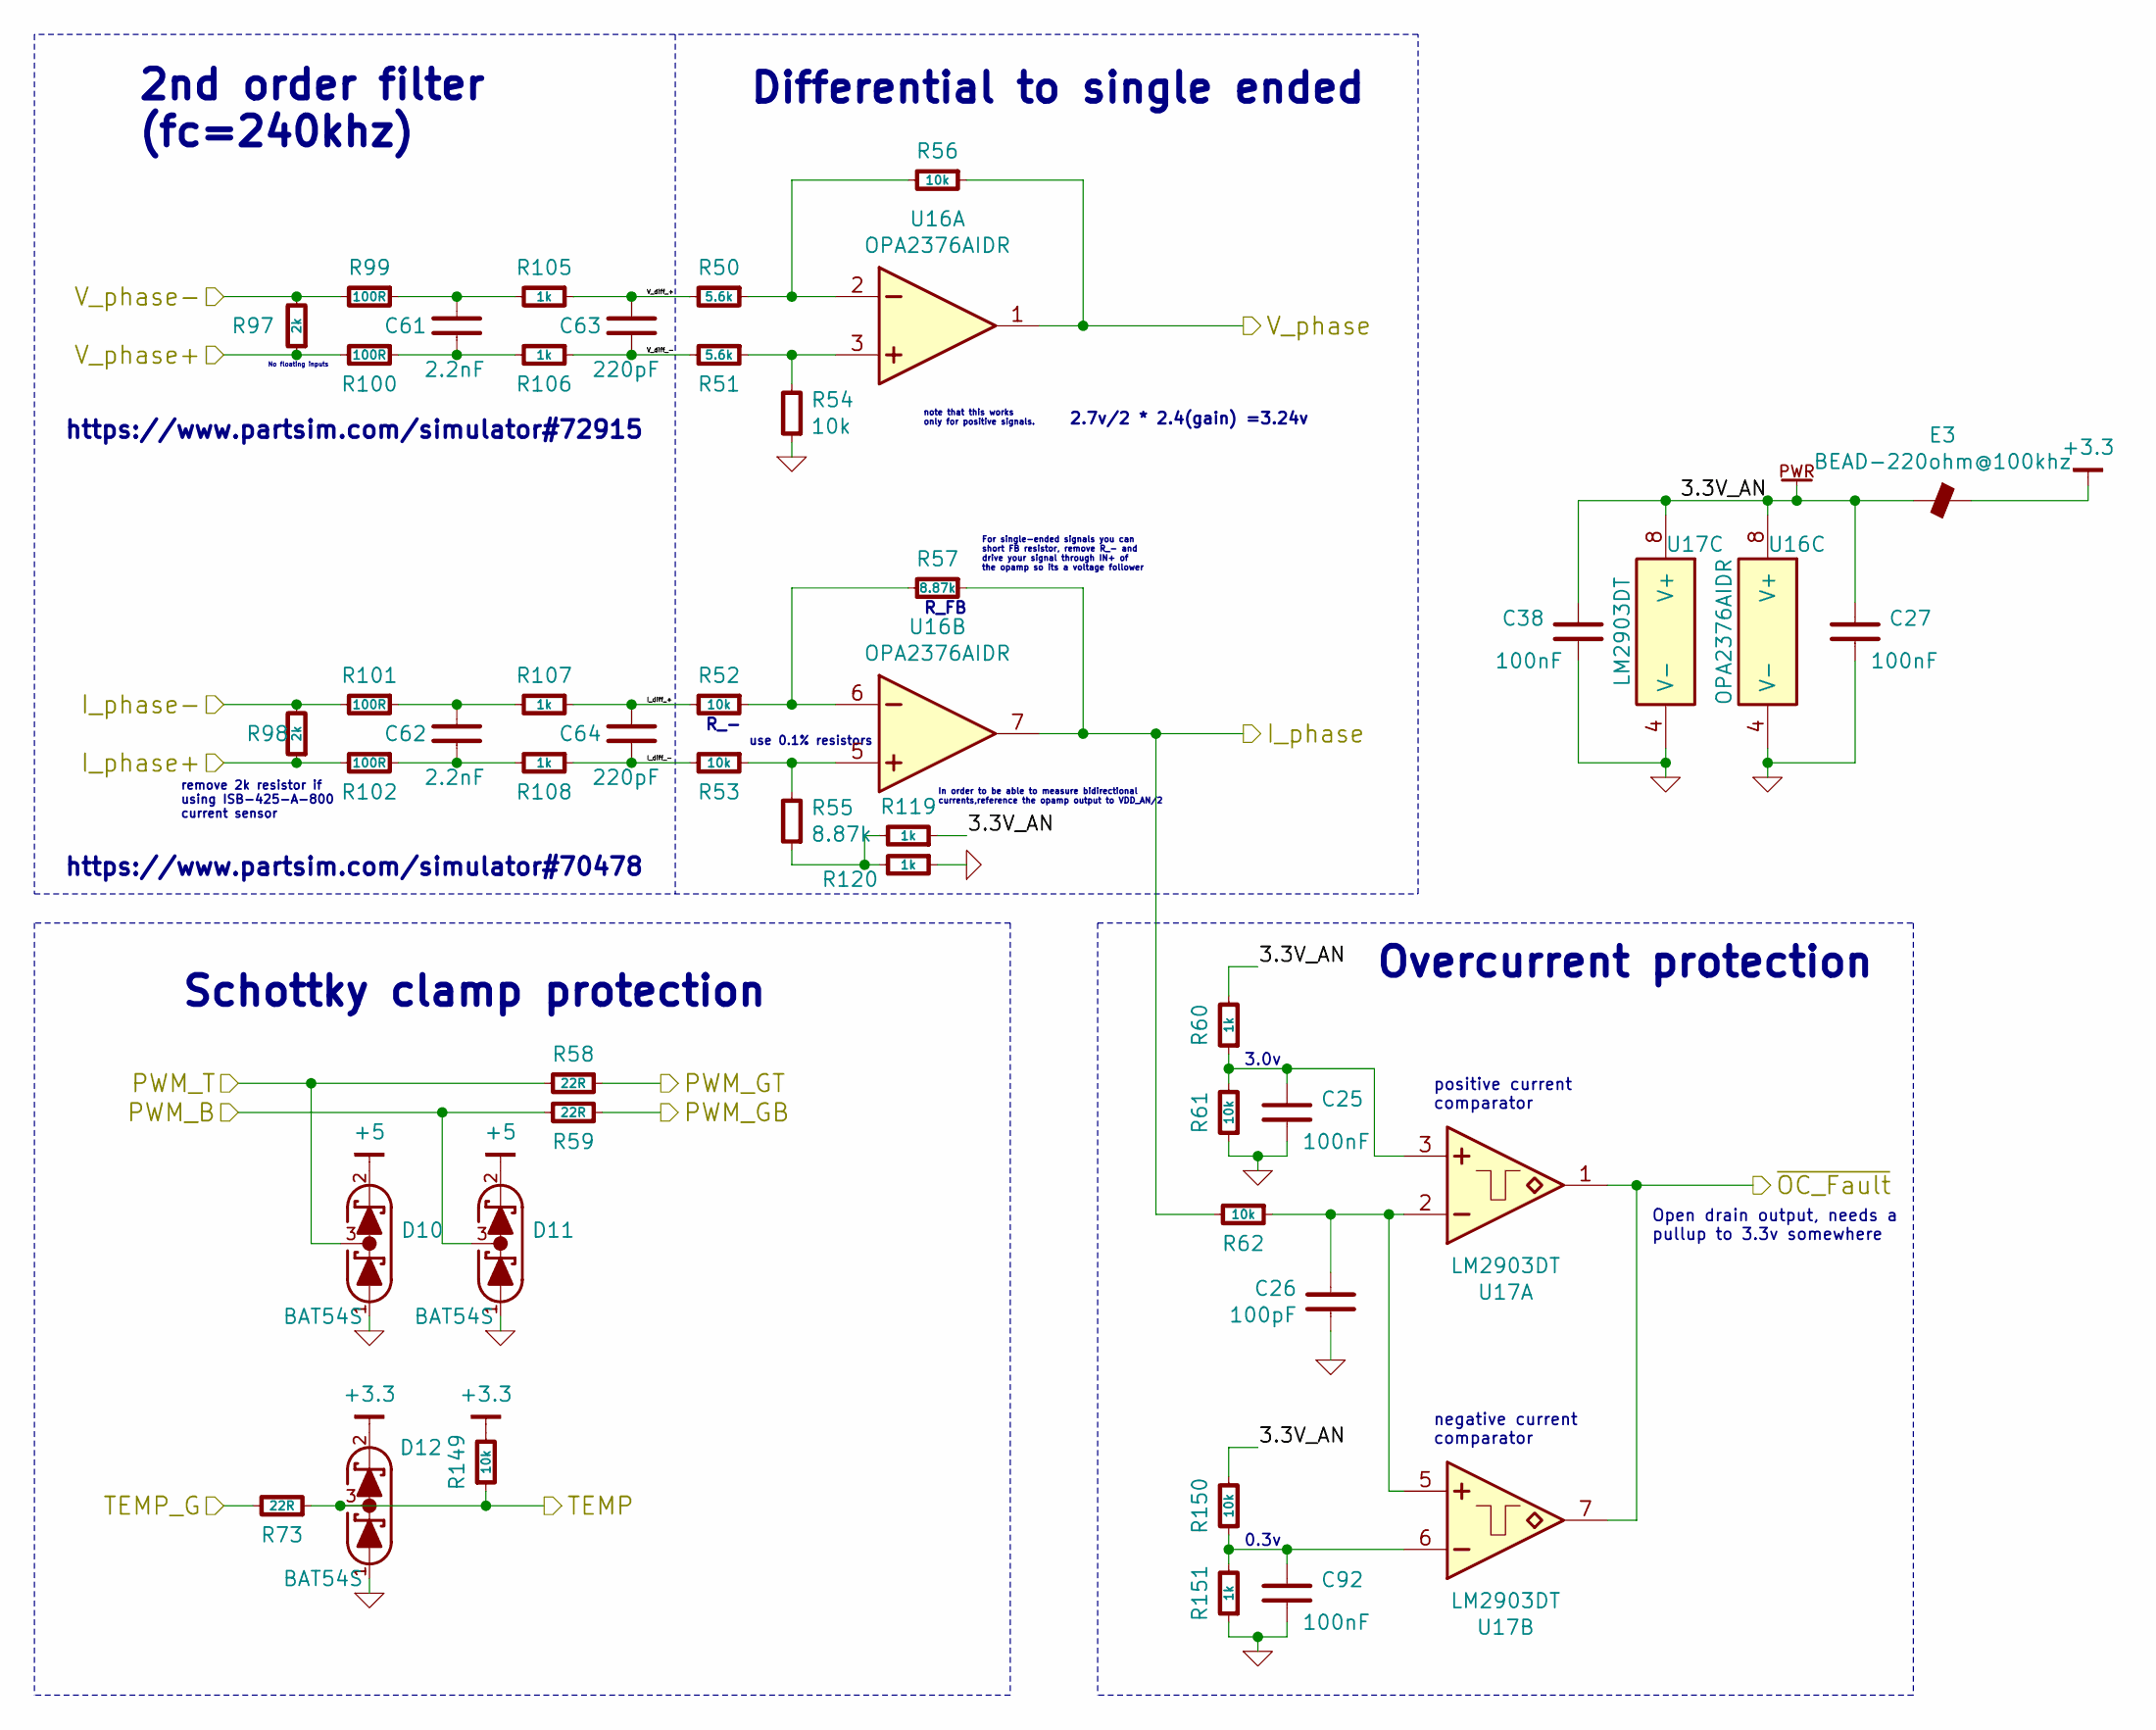
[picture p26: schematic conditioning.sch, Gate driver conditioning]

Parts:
C3, C9, C36, C90: 100nF; CAPC1608X55; MPN GRM188R71E104KA01D
C8: 100pF; CAPC1608X55; MPN C0603C101J5GACTU
C53, C54: 2.2nF; CAPC1608X55
C55, C56: 220pF; CAPC1608X55; MPN GRM1885C1H221JA01D
D4, D5, D6: BAT54S; SOT-23; mfg# TBAT54S,LM
E1: BEAD-220ohm@100khz; INDC2012X130; MPN BLM21PG221SN1D
R4, R5: 5.6k; RESC1608X50; MPN RC0603FR-078K87L
R6, R14, R15, R16, R18, R24, R25, R144: 10k; RESC1608X50; MPN RC0603FR-0710KL
R17, R19: 8.87k; RESC1608X50; MPN RC0603FR-0710KL
R20, R21, R71: 22R; RESC1608X50; MPN RC0603FR-0722RL
R23, R82, R83, R84, R85, R115, R116, R145: 1k; RESC1608X50; MPN RC0603FR-071KL
R76, R77: 2k; RESC1608X50; MPN RC0603FR-072KL
R78, R79, R80, R81: 100R; RESC1608X50; MPN RC0603FR-07100RL
U3: OPA2376AIDR; SOIC127P600X175-8; mfg# OPA2376AIDR
U4: LM2903DT; SOIC127P600X175-8; mfg# LM2903DT

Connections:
+3.3: D6.2 (K), E1.2, R6.2; also elsewhere on the board
/Supervisor/PWM_GUT: D4.3 (COM), R20.2; also elsewhere on the board
/conditioning U/3.3V_AN: C9.1, C36.1, E1.1, R23.2, R115.1, R144.2, U3.8 (V+), U4.8 (V+)
/conditioning U/I_diff_+: C56.1, R14.2, R84.1
/conditioning U/I_diff_-: C56.2, R15.2, R85.1
/conditioning U/I_phase: R19.1, R25.2, U3.7 (OUT); also elsewhere on the board
/conditioning U/I_phase+: R77.1, R81.2; also elsewhere on the board
/conditioning U/I_phase-: R77.2, R80.2; also elsewhere on the board
/conditioning U/PWM_B: D5.3 (COM), R21.2; also elsewhere on the board
/conditioning U/PWM_GB: R21.1; also elsewhere on the board
/conditioning U/PWM_GT: R20.1; also elsewhere on the board
/conditioning U/TEMP: D6.3 (COM), R6.1, R71.1; also elsewhere on the board
/conditioning U/TEMP_G: R71.2; also elsewhere on the board
/conditioning U/V_diff_+: C55.1, R4.2, R82.1
/conditioning U/V_diff_-: C55.2, R5.2, R83.1
/conditioning U/V_phase: R18.1, U3.1 (OUT); also elsewhere on the board
/conditioning U/V_phase+: R76.1, R79.2; also elsewhere on the board
/conditioning U/V_phase-: R76.2, R78.2; also elsewhere on the board
/conditioning U/~OC_Fault: U4.1 (OUT), U4.7 (OUT); also elsewhere on the board
unnamed: C3.1, R23.1, R24.2, U4.3 (IN+)
unnamed: C8.1, R25.1, U4.2 (IN-), U4.5 (IN+)
unnamed: C53.1, R78.1, R82.2
unnamed: C53.2, R79.1, R83.2
unnamed: C54.1, R80.1, R84.2
unnamed: C54.2, R81.1, R85.2
unnamed: C90.1, R144.1, R145.2, U4.6 (IN-)
unnamed: R14.1, R19.2, U3.6 (IN-)
unnamed: R15.1, R17.2, U3.5 (IN+)
unnamed: R5.1, R16.2, U3.3 (IN+)
unnamed: R4.1, R18.2, U3.2 (IN-)
unnamed: R17.1, R115.2, R116.2

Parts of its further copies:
C22, C24, C25, C27, C37, C38, C91, C92: 100nF; CAPC1608X55; MPN GRM188R71E104KA01D
C23, C26: 100pF; CAPC1608X55; MPN C0603C101J5GACTU
C57, C58, C61, C62: 2.2nF; CAPC1608X55
C59, C60, C63, C64: 220pF; CAPC1608X55; MPN GRM1885C1H221JA01D
D7, D8, D9, D10, D11, D12: BAT54S; SOT-23; mfg# TBAT54S,LM
E2, E3: BEAD-220ohm@100khz; INDC2012X130; MPN BLM21PG221SN1D
R34, R35, R50, R51: 5.6k; RESC1608X50; MPN RC0603FR-078K87L
R36, R39, R40, R42, R47, R48, R52, R53, R54, R56, R61, R62, R146, R147, R149, R150: 10k; RESC1608X50; MPN RC0603FR-0710KL
R41, R43, R55, R57: 8.87k; RESC1608X50; MPN RC0603FR-0710KL
R44, R45, R58, R59, R72, R73: 22R; RESC1608X50; MPN RC0603FR-0722RL
R46, R60, R93, R94, R95, R96, R105, R106, R107, R108, R117, R118, R119, R120, R148, R151: 1k; RESC1608X50; MPN RC0603FR-071KL
R87, R88, R97, R98: 2k; RESC1608X50; MPN RC0603FR-072KL
R89, R90, R91, R92, R99, R100, R101, R102: 100R; RESC1608X50; MPN RC0603FR-07100RL
U10, U17: LM2903DT; SOIC127P600X175-8; mfg# LM2903DT
U12, U16: OPA2376AIDR; SOIC127P600X175-8; mfg# OPA2376AIDR

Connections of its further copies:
+3.3: D9.2 (K), D12.2 (K), E2.2, E3.2, R146.2, R149.2; also elsewhere on the board
/Supervisor/PWM_GVT: D7.3 (COM), R44.2; also elsewhere on the board
/Supervisor/PWM_GWT: D10.3 (COM), R58.2; also elsewhere on the board
/conditioning U/~OC_Fault: U10.1 (OUT), U10.7 (OUT), U17.1 (OUT), U17.7 (OUT); also elsewhere on the board
/conditioning V/3.3V_AN: C24.1, C37.1, E2.1, R46.2, R117.1, R147.2, U10.8 (V+), U12.8 (V+)
/conditioning V/I_diff_+: C60.1, R36.2, R95.1
/conditioning V/I_diff_-: C60.2, R39.2, R96.1
/conditioning V/I_phase: R43.1, R48.2, U12.7 (OUT); also elsewhere on the board
/conditioning V/I_phase+: R88.1, R92.2; also elsewhere on the board
/conditioning V/I_phase-: R88.2, R91.2; also elsewhere on the board
/conditioning V/PWM_B: D8.3 (COM), R45.2; also elsewhere on the board
/conditioning V/PWM_GB: R45.1; also elsewhere on the board
/conditioning V/PWM_GT: R44.1; also elsewhere on the board
/conditioning V/TEMP: D9.3 (COM), R72.1, R146.1; also elsewhere on the board
/conditioning V/TEMP_G: R72.2; also elsewhere on the board
/conditioning V/V_diff_+: C59.1, R34.2, R93.1
/conditioning V/V_diff_-: C59.2, R35.2, R94.1
/conditioning V/V_phase: R42.1, U12.1 (OUT); also elsewhere on the board
/conditioning V/V_phase+: R87.1, R90.2; also elsewhere on the board
/conditioning V/V_phase-: R87.2, R89.2; also elsewhere on the board
/conditioning W/3.3V_AN: C27.1, C38.1, E3.1, R60.2, R119.1, R150.2, U16.8 (V+), U17.8 (V+)
/conditioning W/I_diff_+: C64.1, R52.2, R107.1
/conditioning W/I_diff_-: C64.2, R53.2, R108.1
/conditioning W/I_phase: R57.1, R62.2, U16.7 (OUT); also elsewhere on the board
/conditioning W/I_phase+: R98.1, R102.2; also elsewhere on the board
/conditioning W/I_phase-: R98.2, R101.2; also elsewhere on the board
/conditioning W/PWM_B: D11.3 (COM), R59.2; also elsewhere on the board
/conditioning W/PWM_GB: R59.1; also elsewhere on the board
/conditioning W/PWM_GT: R58.1; also elsewhere on the board
/conditioning W/TEMP: D12.3 (COM), R73.1, R149.1; also elsewhere on the board
/conditioning W/TEMP_G: R73.2; also elsewhere on the board
/conditioning W/V_diff_+: C63.1, R50.2, R105.1
/conditioning W/V_diff_-: C63.2, R51.2, R106.1
/conditioning W/V_phase: R56.1, U16.1 (OUT); also elsewhere on the board
/conditioning W/V_phase+: R97.1, R100.2; also elsewhere on the board
/conditioning W/V_phase-: R97.2, R99.2; also elsewhere on the board
unnamed: C22.1, R46.1, R47.2, U10.3 (IN+)
unnamed: C23.1, R48.1, U10.2 (IN-), U10.5 (IN+)
unnamed: C25.1, R60.1, R61.2, U17.3 (IN+)
unnamed: C26.1, R62.1, U17.2 (IN-), U17.5 (IN+)
unnamed: C57.1, R89.1, R93.2
unnamed: C57.2, R90.1, R94.2
unnamed: C58.1, R91.1, R95.2
unnamed: C58.2, R92.1, R96.2
unnamed: C61.1, R99.1, R105.2
unnamed: C61.2, R100.1, R106.2
unnamed: C62.1, R101.1, R107.2
unnamed: C62.2, R102.1, R108.2
unnamed: C91.1, R147.1, R148.2, U10.6 (IN-)
unnamed: C92.1, R150.1, R151.2, U17.6 (IN-)
unnamed: R34.1, R42.2, U12.2 (IN-)
unnamed: R35.1, R40.2, U12.3 (IN+)
unnamed: R36.1, R43.2, U12.6 (IN-)
unnamed: R39.1, R41.2, U12.5 (IN+)
unnamed: R50.1, R56.2, U16.2 (IN-)
unnamed: R51.1, R54.2, U16.3 (IN+)
unnamed: R52.1, R57.2, U16.6 (IN-)
unnamed: R53.1, R55.2, U16.5 (IN+)
unnamed: R41.1, R117.2, R118.2
unnamed: R55.1, R119.2, R120.2

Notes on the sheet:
Overcurrent protection
Differential to single ended
Schottky clamp protection
2nd order filter (fc=240khz)
No floating inputs
note that this works only for positive signals.
In order to be able to measure bidirectional currents,reference the opamp output to VDD_AN/2
For single-ended signals you can short FB resistor, remove R_- and drive your signal through IN+ of the opamp so its a voltage follower
R_FB
R_-
https://www.partsim.com/simulator#70478
2.7v/2 * 2.4(gain) =3.24v
https://www.partsim.com/simulator#72915
use 0.1% resistors
remove 2k resistor if using ISB-425-A-800 current sensor
positive current comparator
negative current comparator
0.3v
3.0v
Open drain output, needs a pullup to 3.3v somewhere

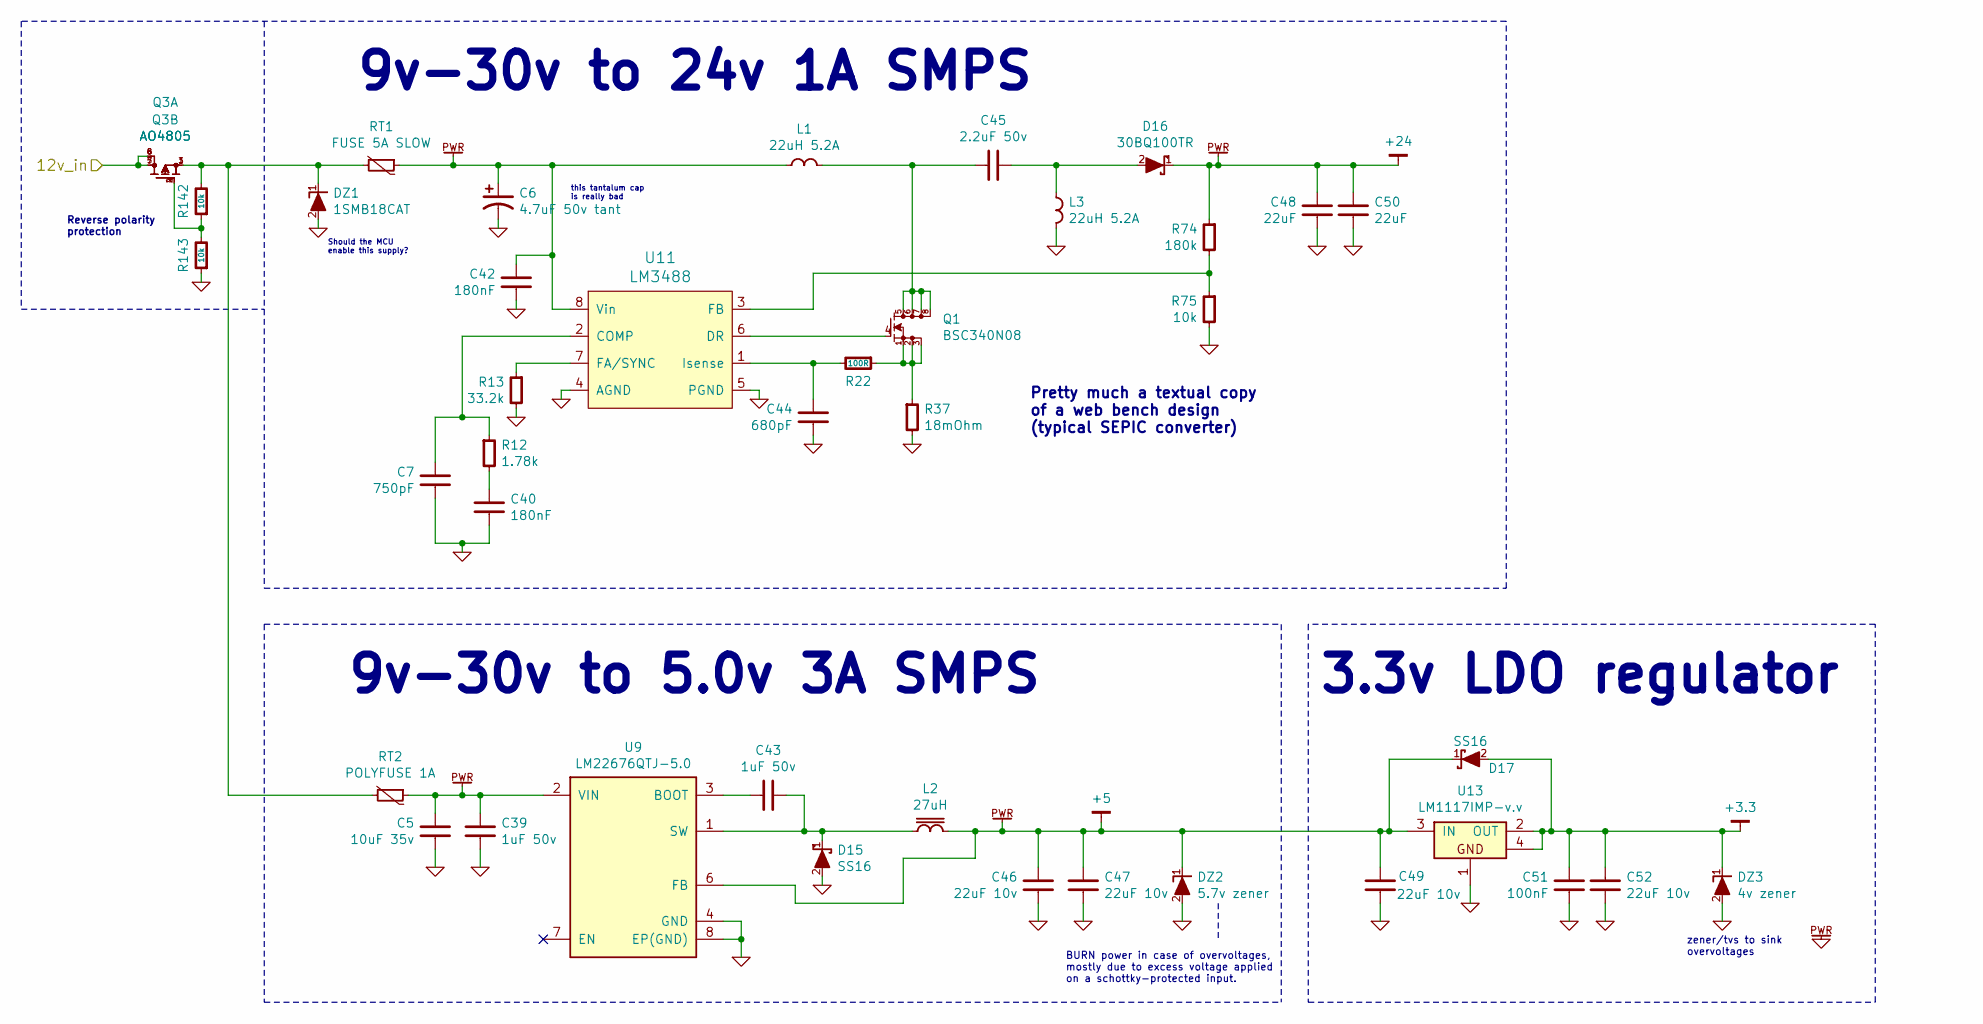
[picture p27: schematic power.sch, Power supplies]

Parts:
C5: 10uF 35v; CAPC3216X70; MPN GMK316AB7106KL-TR
C6: 4.7uF 50v tant; CAPMP7343X310; mfg# 593D475X9050D2TE3
C7: 750pF; CAPC2012X70; mfg# CL21C751JBCNNNC
C39, C43: 1uF 50v; CAPC2012X70; MPN UMK212B7105KG-T
C40, C42: 180nF; CAPC1608X55; MPN GRM188R71E184KA88D
C44: 680pF; CAPC2012X70; mfg# CL21C751JBCNNNC
C45: 2.2uF 50v; CAPC3216X70; mfg# GRM31CR71H225KA88L
C46, C47, C49, C52: 22uF 10v; CAPC3216X70; mfg# LMK316AB7226ML-TR
C48, C50: 22uF; CAPC2012X70; mfg# C2012X5R1V226M125AC
C51: 100nF; CAPC1608X55; MPN GRM188R71E104KA01D
D15, D17: SS16; DIOM5326X292; MPN SS16
D16: 30BQ100TR; DIOM7959X265; mfg# 30BQ100TR
DZ1: 1SMB18CAT; do214aa; mfg# 1SMB18CAT3GOSCT-ND
DZ2: 5.7v zener; DIOM5226X203; MPN 1SMA59xxBT3G
DZ3: 4v zener; DIOM5226X203
L1, L3: 22uH 5.2A; BOURNS-SRR1210; mfg# SRR1210-220M
L2: 27uH; BOURNS-SDR1307; mfg# SDR1307-270ML
Q1: BSC340N08; TEXAS-Q5A; mfg# BSC340N08NS3GATMA1
Q3: AO4805; SOIC127P600X175-8; MPN AO4805
R12: 1.78k; RESC1608X50; MPN RC0603FR-071K78L
R13: 33.2k; RESC1608X50; MPN RC0603FR-0733K2L
R22: 100R; RESC1608X50; MPN RC0603FR-07100RL
R37: 18mOhm; CAPC1632X76; mfg# PRL1632-R018-F-T1
R74: 180k; RESC1608X50; MPN RC0603FR-07180KL
R75, R142, R143: 10k; RESC1608X50; MPN RC0603FR-0710KL
RT1: FUSE 5A SLOW; RESC3216X60; MPN C1S 5
RT2: POLYFUSE 1A; RESC3216X60; MPN 0ZCJ0050AF2E
U9: LM22676QTJ-5.0; TO-263-7-TEXAS; MPN LM22676QTJE-5.0/NOPB
U11: LM3488; SOP65P490X109-8; MPN LM3488MM/NOPB
U13: LM1117IMP-v.v; SOT-223; MPN LM1117IMP-3.3/NOPB

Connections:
+3.3: C51.1, C52.2, D17.2 (A), DZ3.1 (K), U13.2 (OUT), U13.4; also elsewhere on the board
/Power/12v_in: Q3.5 (D1A), Q3.6 (D1B), Q3.7 (D2A), Q3.8 (D2B); also elsewhere on the board
unnamed: C7.1, R12.1, U11.2 (COMP)
unnamed: C40.1, R12.2
unnamed: C43.1, D15.1 (K), L2.2, U9.1 (SW)
unnamed: C43.2, U9.3 (BOOT)
unnamed: C44.1, R22.2, U11.1 (Isense)
unnamed: C45.1, D16.2 (A), L3.2
unnamed: C45.2, L1.1, Q1.5 (D), Q1.6 (D), Q1.7 (D), Q1.8 (D)
unnamed: DZ1.1 (K), Q3.1 (S2), Q3.3 (S1), R142.2, RT1.2, RT2.2
unnamed: Q1.1 (S), Q1.2 (S), Q1.3 (S), R22.1, R37.1
unnamed: Q1.4 (G), U11.6 (DR)
unnamed: Q3.2 (G1), Q3.4 (G1), R142.1, R143.2
unnamed: R13.1, U11.7 (FA/SYNC)
unnamed: R74.2, R75.1, U11.3 (FB)

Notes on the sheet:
9v-30v to 24v 1A SMPS
Pretty much a textual copy of a web bench design (typical SEPIC converter)
9v-30v to 5.0v 3A SMPS
3.3v LDO regulator
Should the MCU enable this supply?
Reverse polarity protection
this tantalum cap is really bad
zener/tvs to sink overvoltages
BURN power in case of overvoltages, mostly due to excess voltage applied on a schottky-protected input.

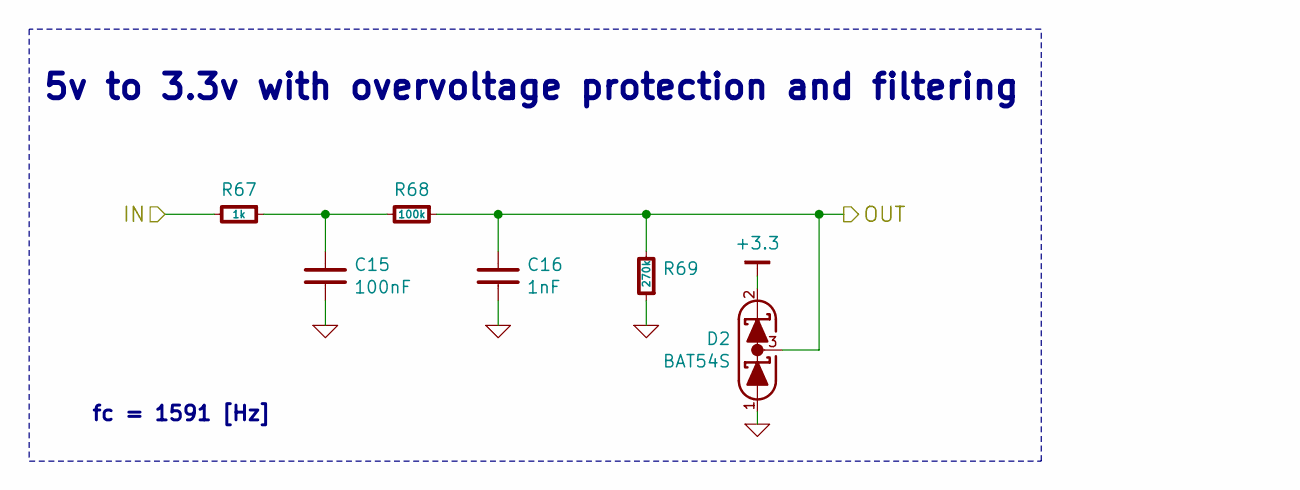
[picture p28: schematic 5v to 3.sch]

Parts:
C13: 100nF; CAPC1608X55; MPN GRM188R71E104KA01D
C14: 1nF; CAPC1608X55; MPN GRM188R71H102KA01D
D1: BAT54S; SOT-23; mfg# TBAT54S,LM
R64: 1k; RESC1608X50; MPN RC0603FR-071KL
R65: 100k; RESC1608X50; MPN RC0603FR-07100KL
R66: 270k; RESC1608X50; MPN RC0603FR-07270KL

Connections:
+3.3: D1.2 (K); also elsewhere on the board
/Accel input conditioning/IN: R64.2; also elsewhere on the board
/STM32F4/ADC_15: C14.1, D1.3 (COM), R65.1, R66.2; also elsewhere on the board
unnamed: C13.1, R64.1, R65.2

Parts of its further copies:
C15: 100nF; CAPC1608X55; MPN GRM188R71E104KA01D
C16: 1nF; CAPC1608X55; MPN GRM188R71H102KA01D
D2: BAT54S; SOT-23; mfg# TBAT54S,LM
R67: 1k; RESC1608X50; MPN RC0603FR-071KL
R68: 100k; RESC1608X50; MPN RC0603FR-07100KL
R69: 270k; RESC1608X50; MPN RC0603FR-07270KL

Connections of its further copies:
+3.3: D2.2 (K); also elsewhere on the board
/Regen input conditioning/IN: R67.2; also elsewhere on the board
/STM32F4/ADC_8: C16.1, D2.3 (COM), R68.1, R69.2; also elsewhere on the board
unnamed: C15.1, R67.1, R68.2

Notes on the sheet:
5v to 3.3v with overvoltage protection and filtering
fc = 1591 [Hz]

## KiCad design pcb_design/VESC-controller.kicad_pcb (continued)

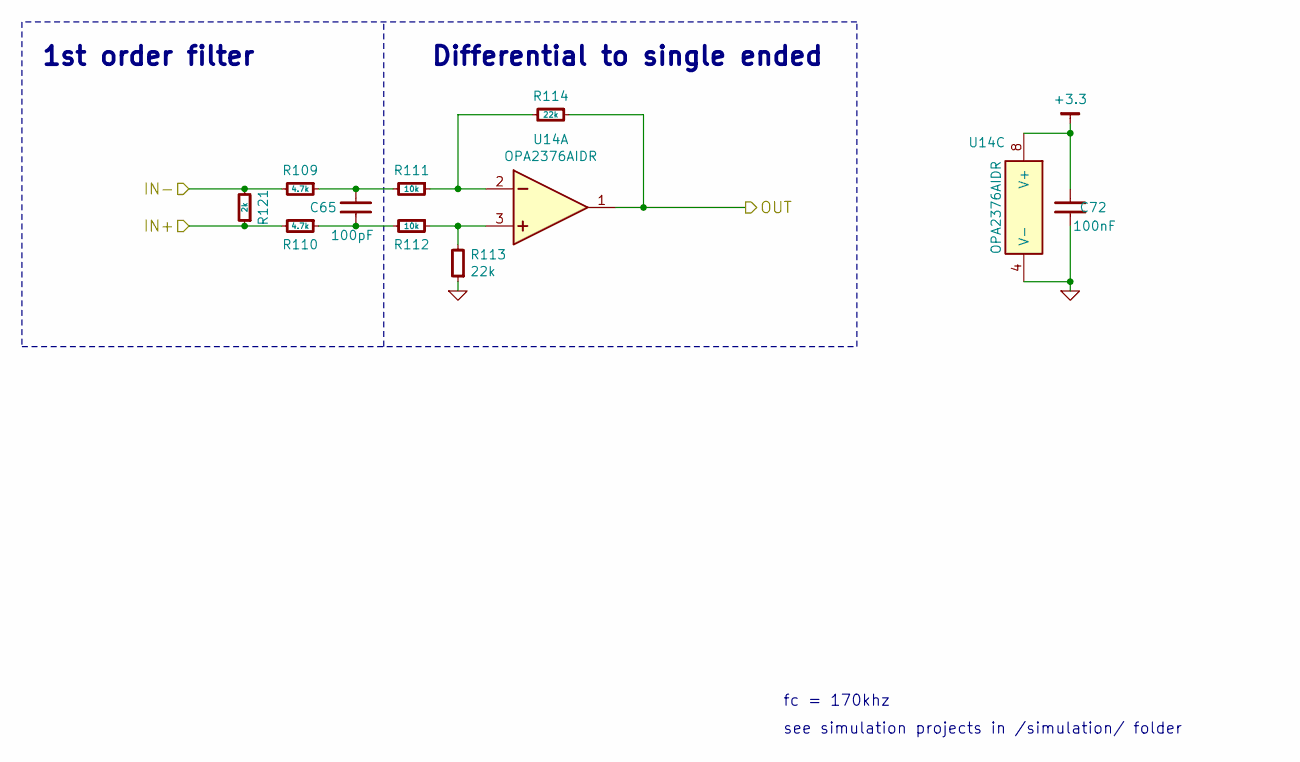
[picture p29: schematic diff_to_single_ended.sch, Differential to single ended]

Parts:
C65: 100pF; CAPC1608X55; MPN C0603C101J5GACTU
C72: 100nF; CAPC1608X55; MPN GRM188R71E104KA01D
R109, R110: 4.7k; RESC1608X50; MPN RC0603FR-074K7L
R111, R112: 10k; RESC1608X50; MPN RC0603FR-0710KL
R113, R114: 22k; RESC1608X50; MPN RC0603FR-0722KL
R121: 2k; RESC1608X50; MPN RC0603FR-072KL
U14: OPA2376AIDR; SOIC127P600X175-8; MPN OPA2376AIDR

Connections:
+3.3: C72.1, U14.8 (V+); also elsewhere on the board
/V_bus+: R110.2, R121.1; also elsewhere on the board
/V_bus-: R109.2, R121.2; also elsewhere on the board
/Vbus_conditioning/OUT: R114.1, U14.1 (OUT); also elsewhere on the board
unnamed: C65.1, R109.1, R111.2
unnamed: C65.2, R110.1, R112.2
unnamed: R111.1, R114.2, U14.2 (IN-)
unnamed: R112.1, R113.2, U14.3 (IN+)

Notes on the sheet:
Differential to single ended
1st order filter
fc = 170khz
see simulation projects in /simulation/ folder

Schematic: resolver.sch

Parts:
C73, C74, C75, C77, C81, C82, C85, C86, C87: 100nF; CAPC1608X55; MPN GRM188R71E104KA01D
C76, C78: 2.2uF; CAPC1608X55; MPN GRM188R71A225KE15D
C79, C80: 15pF; CAPC1608X55; MPN GCM1885C1H150JA16D
C83, C84: 120pF; CAPC1608X55; MPN C0603C121F5GACTU
C88, C89: 22uF; CAPC2012X70; mfg# C2012X5R1V226M125AC
E5, E6: BEAD-220ohm@100khz; INDC2012X130; mfg# BLM21PG221SN1D
R124, R125: 68.1k; RESC1608X50; MPN RC0603FR-0768K1L
R126, R128, R130, R131: 10k; RESC1608X50; MPN RC0603FR-0710KL
R127, R129: 22k; RESC1608X50; MPN RC0603FR-0722KL
R132, R133: 15.4k; RESC1608X50; MPN RC0603FR-0715K4L
R136, R137: 0R; RESC1608X50; MPN RC0603JR-070RL
U15: AD2S1205; QFP80P1200X1200X160-44; mfg# AD2S1205
U18: SN74LVC1G; SC-70-6; mfg# SN74LVC1G11IDCKRQ1
U19: AD8397; SOIC127P600X175-8; mfg# AD8397ARZ
U20: APX809; SOT-23; mfg# APX809-46SRG-7
U21: NCV78Mxx; TO-252; mfg# NCV78M12BDTRKG
X1: ABM3B - 8MHz; OSCCC320X500X150; mfg# ABM3B-8.000MHZ-10-1UT

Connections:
+3.3: C75.1, U18.5 (VCC); also elsewhere on the board
+12: C85.1, C88.1, C89.1, E6.2, R127.2, R129.2, U19.8 (V+)
/STM32F4/PB3: U15.4 (~SAMPLE); also elsewhere on the board
/STM32F4/PC12: U15.5 (~RDVEL); also elsewhere on the board
/STM32F4/PD2: U18.4 (QA); also elsewhere on the board
/STM32F4/SPI3_NSS: U15.2 (RD), U15.3 (~CS); also elsewhere on the board
/resolver/CLK: U15.8 (DB10/SCLK); also elsewhere on the board
/resolver/COS+: R125.1, U15.41 (Cos); also elsewhere on the board
/resolver/COS-: R125.2, U15.40 (CosLO); also elsewhere on the board
/resolver/EXC+: C83.1, R132.1, U19.7 (OUT); also elsewhere on the board
/resolver/EXC-: C84.1, R133.1, U19.1 (OUT); also elsewhere on the board
/resolver/EXC_SOURCE+: R126.2, U15.34 (EXC)
/resolver/EXC_SOURCE-: R128.2, U15.35 (~EXC)
/resolver/MISO: U15.7 (DB11/SO); also elsewhere on the board
/resolver/SIN+: R124.1, U15.37 (Sin); also elsewhere on the board
/resolver/SIN-: R124.2, U15.38 (SinLO); also elsewhere on the board
unnamed: C77.1, C78.1, E5.1, U15.39 (AVDD)
unnamed: C79.1, U15.22 (CLKIN), X1.1
unnamed: C80.1, U15.21 (XTALOUT), X1.3
unnamed: C81.1, R129.1, R131.2, U19.3 (IN+)
unnamed: C82.1, R127.1, R130.2, U19.5 (IN+)
unnamed: C83.2, R126.1, R132.2, U19.6 (IN-)
unnamed: C84.2, R128.1, R133.2, U19.2 (IN-)
unnamed: C87.1, E6.1, U21.2 (OUT)
unnamed: R136.2, U15.31 (FS1)
unnamed: R137.2, U15.32 (FS2)
unnamed: U15.6 (~SOE), U18.1 (D1A)
unnamed: U15.29 (~DOS), U18.3 (D2A)
unnamed: U15.30 (~LOT), U18.6 (D3A)
unnamed: U15.33 (~RESET), U20.2

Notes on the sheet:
Resolver interface
Buffer
This is an alternative buffer suggested here: http://www.analog.com/en/analog-dialogue/articles/precision-rtdc-measures-angular-position-and-velocity.html It seems to invert the signal... Its more expensive, but much simpler and smaller
RESET line requires a voltage monitor

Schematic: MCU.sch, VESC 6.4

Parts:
C10, C11, C12, C30, C32, C34: 100nF; CAPC1608X55; MPN GRM188R71E104KA01D
C17, C33: 15pF; CAPC1608X55; MPN GCM1885C1H150JA16D
C28, C29, C31: 2.2uF; CAPC1608X55; MPN GRM188R71A225KE15D
E4: BEAD-220ohm@100khz; INDC2012X130; MPN BLM21PG221SN1D
J9: SWD; CONN-100MIL-M-1x5
R122: 1k; RESC1608X50; MPN RC0603FR-071KL
SW1: BOOTLOADER; SMD-Switch_B3U-1000-B; mfg# B3U-1000P
U1: STM32F40X_LQFP64; QFP50P1200X1200X100-64; MPN STM32F405RGT6
X2: ABM3B - 8MHz; OSCCC320X500X150; mfg# ABM3B-8.000MHZ-10-1UT

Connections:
+3.3: C10.1, C11.1, C12.1, C34.1, E4.2, J9.1, SW1.2, U1.1 (VBAT), U1.19 (VDD), U1.32 (VDD), U1.48 (VDD), U1.64 (VDD); also elsewhere on the board
+3.3A: C30.1, C31.1, E4.1, U1.13 (VDDA); also elsewhere on the board
/Filters/HALL1_OUT: U1.37 (PC6); also elsewhere on the board
/Filters/HALL2_OUT: U1.38 (PC7); also elsewhere on the board
/Filters/HALL3_OUT: U1.39 (PC8); also elsewhere on the board
/Filters/TEMP_IN: U1.24 (PC4(ADC12_IN14)); also elsewhere on the board
/Isolated CAN/CAN_RX: U1.61 (PB8); also elsewhere on the board
/Isolated CAN/CAN_TX: U1.62 (PB9); also elsewhere on the board
/Protected GPIOs/IN1: U1.58 (PB6); also elsewhere on the board
/Protected GPIOs/IN2: U1.23 (PA7(ADC12_IN7)); also elsewhere on the board
/STM32F4/ADC_8: U1.26 (PB0(ADC12_IN8)); also elsewhere on the board
/STM32F4/ADC_15: U1.25 (PC5(ADC12_IN15)); also elsewhere on the board
/STM32F4/ADC_TEMP: U1.17 (PA3(ADC123_IN3)); also elsewhere on the board
/STM32F4/LED_GREEN: U1.28 (PB2-BOOT1); also elsewhere on the board
/STM32F4/LED_RED: U1.27 (PB1(ADC12_IN9)); also elsewhere on the board
/STM32F4/NRST: C32.1, J9.5, U1.7 (NRST)
/STM32F4/PB3: U1.55 (PB3(JTDO/TRACESWO)); also elsewhere on the board
/STM32F4/PB4: U1.56 (PB4(NJTRST)); also elsewhere on the board
/STM32F4/PC9: U1.40 (PC9); also elsewhere on the board
/STM32F4/PC12: U1.53 (PC12); also elsewhere on the board
/STM32F4/PD2: U1.54 (PD2); also elsewhere on the board
/STM32F4/PWM_UB: U1.34 (PB13(OTG_HS_VBUS)); also elsewhere on the board
/STM32F4/PWM_UT: U1.41 (PA8); also elsewhere on the board
/STM32F4/PWM_VB: U1.35 (PB14); also elsewhere on the board
/STM32F4/PWM_VT: U1.42 (PA9(OTG_FS_VBUS)); also elsewhere on the board
/STM32F4/PWM_WB: U1.36 (PB15); also elsewhere on the board
/STM32F4/PWM_WT: U1.43 (PA10); also elsewhere on the board
/STM32F4/RX_SDA_NSS: U1.30 (PB11); also elsewhere on the board
/STM32F4/SPI3_NSS: U1.50 (PA15(JTDI)); also elsewhere on the board
/STM32F4/SWCLK: J9.2, U1.49 (PA14(JTCK-SWCLK))
/STM32F4/SWDIO: J9.4, U1.46 (PA13(JTMS-SWDIO))
/STM32F4/TX_SCL_MOSI: U1.29 (PB10); also elsewhere on the board
/STM32F4/USB_D+: U1.45 (PA12); also elsewhere on the board
/STM32F4/USB_D-: U1.44 (PA11); also elsewhere on the board
/STM32F4/~DRIVER_RESET: U1.3 (PC14-OSC32_IN); also elsewhere on the board
/STM32F4/~FAULT: U1.33 (PB12); also elsewhere on the board
/Supervisor/CLR_OC_Fault: U1.57 (PB5); also elsewhere on the board
/Supervisor/OC_Fault: U1.59 (PB7); also elsewhere on the board
/Vbus_conditioning/OUT: U1.11 (PC3(ADC123_IN13)); also elsewhere on the board
/conditioning U/I_phase: U1.8 (PC0(ADC123_IN10)); also elsewhere on the board
/conditioning U/TEMP: U1.20 (PA4(ADC12_IN4/DAC1_OUT)); also elsewhere on the board
/conditioning U/V_phase: U1.14 (PA0(ADC123_IN0/WKUP)); also elsewhere on the board
/conditioning V/I_phase: U1.9 (PC1(ADC123_IN11)); also elsewhere on the board
/conditioning V/TEMP: U1.21 (PA5(ADC12_IN5/DAC2_OUT)); also elsewhere on the board
/conditioning V/V_phase: U1.15 (PA1(ADC123_IN1)); also elsewhere on the board
/conditioning W/I_phase: U1.10 (PC2(ADC123_IN12)); also elsewhere on the board
/conditioning W/TEMP: U1.22 (PA6(ADC12_IN6)); also elsewhere on the board
/conditioning W/V_phase: U1.16 (PA2(ADC123_IN2)); also elsewhere on the board
/resolver/CLK: U1.51 (PC10); also elsewhere on the board
/resolver/MISO: U1.52 (PC11); also elsewhere on the board
unnamed: C17.2, U1.5 (PH0-OSC_IN), X2.1
unnamed: C28.2, U1.31 (VCAP1)
unnamed: C29.2, U1.47 (VCAP2)
unnamed: C33.2, U1.6 (PH1-OSC_OUT), X2.3
unnamed: R122.1, SW1.1, U1.60 (BOOT0(VPP))

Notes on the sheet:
Bypass, place next to VDD pins
vesc vanilla uses PB7!
remember it should be pulled down if you want to enter bootloader
PIN ---------------------------------- FAULT SPI_CS LED_GREEN ACCEL REGEN GATE DRIVER RST
| VESC Vanilla | PB7 | PC9 (drv) | PB0 | - | - | -
| VESC-controller | PB12 (could enable BRK) | PA15 (resolver) | PB2 | PC5 (AN15) | PB0 (AN8) | PC14
Changes for board support package
STM32F405 MCU

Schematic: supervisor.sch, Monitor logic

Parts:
C18, C19, C20, C21: 100nF; CAPC1608X55; MPN GRM188R71E104KA01D
C93: 220pF; CAPC1608X55; MPN GRM1885C1H221JA01D
D19: BAT54S; SOT-23; mfg# TBAT54S,LM
DS3: OCP; LED-0603; MPN LTST-C191KRKT
DS6: FAULT; LED-0603; MPN LTST-C191KRKT
R26, R27, R28, R29, R30, R31, R32, R33: 4.7k; RESC1608X50; MPN RC0603FR-074K7L
R86, R141: 100R; RESC1608X50; MPN RC0603FR-07100RL
R123: 22R; RESC1608X50; MPN RC0603FR-0722RL
R138: 10k; RESC1608X50; MPN RC0603FR-0710KL
U5: 7400-TSSOP; SOP65P640X110-14; MPN SN74LVC00APWR
U6: SN74ACT08PWR; SOP65P640X110-14; mfg# SN74ACT08PWR
U7: SN74ACT08PWR; SOP65P640X110-14; MPN SN74ACT08PWR
U8: SN74AUP1G74; SOP50P310X100-8; MPN SN74AUP1G74DCUR

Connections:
+3.3: C18.2, C21.2, D19.2 (K), DS6.2 (A), R26.1, R33.1, R86.1, R138.2, U5.14 (V+), U8.2 (D), U8.7 (~PRE), U8.8 (VCC); also elsewhere on the board
/STM32F4/PWM_UB: R30.1, U5.2 (D2A), U6.5 (D2B); also elsewhere on the board
/STM32F4/PWM_UT: R27.1, U5.1 (D1A), U6.1 (D1A); also elsewhere on the board
/STM32F4/PWM_VB: R31.1, U5.5 (D2B), U6.13 (D2D); also elsewhere on the board
/STM32F4/PWM_VT: R28.1, U5.4 (D1B), U6.9 (D1C); also elsewhere on the board
/STM32F4/PWM_WB: R32.1, U5.10 (D2C), U7.5 (D2B); also elsewhere on the board
/STM32F4/PWM_WT: R29.1, U5.9 (D1C), U7.1 (D1A); also elsewhere on the board
/STM32F4/~DRIVER_RESET: U7.9 (D1C); also elsewhere on the board
/STM32F4/~FAULT: C93.1, D19.3 (COM), R123.1, R141.2, U7.10 (D2C); also elsewhere on the board
/Supervisor/CLR_OC_Fault: U8.6 (~CLR); also elsewhere on the board
/Supervisor/OC_Fault: U8.5 (Q); also elsewhere on the board
/Supervisor/PWM_GUT: U6.3 (QA); also elsewhere on the board
/Supervisor/PWM_GVT: U6.8 (QC); also elsewhere on the board
/Supervisor/PWM_GWT: U7.3 (QA); also elsewhere on the board
/conditioning U/PWM_B: U6.6 (QB); also elsewhere on the board
/conditioning U/~OC_Fault: R26.2, U5.13 (D2D); also elsewhere on the board
/conditioning V/PWM_B: U6.11 (QD); also elsewhere on the board
/conditioning W/PWM_B: U7.6 (QB); also elsewhere on the board
unnamed: DS3.1 (K), U7.13 (D2D), U8.3 (~Q)
unnamed: DS3.2 (A), R86.2
unnamed: DS6.1 (K), R141.1
unnamed: R33.2, U5.12 (D1D)
unnamed: U5.3 (QA), U6.2 (D2A), U6.4 (D1B)
unnamed: U5.6 (QB), U6.10 (D2C), U6.12 (D1D)
unnamed: U5.8 (QC), U7.2 (D2A), U7.4 (D1B)
unnamed: U5.11 (QD), U8.1 (CLK)
unnamed: U7.8 (QC), U7.12 (D1D)
~DRIVER_RESET: U7.11 (QD); also elsewhere on the board
~FAULT: R123.2, R138.1; also elsewhere on the board

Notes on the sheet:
PWM overlap elimination
AND: 2.9ns propagation delay
Overcurrent latch
If FAULT, or OCP, or RESET is triggered, RESET driver
pulldowns to assert MCU pins in high-Z state during boot

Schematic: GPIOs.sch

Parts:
DZ4, DZ5: MMSZ52XXB; SOD-123
Q4, Q5: SI2302; SOT-23; MPN SI2302
R152, R153: 1k; RESC1608X50; MPN RC0603FR-071KL
R154, R155, R156, R157: NI; RESC1608X50; MPN RC0603FR-071KL

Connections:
/Protected GPIOs/IN1: Q4.1 (G), R152.2, R154.1; also elsewhere on the board
/Protected GPIOs/IN2: Q5.1 (G), R153.2, R155.1; also elsewhere on the board
/Protected GPIOs/OUT1: DZ4.1 (K), Q4.3 (D), R154.2, R156.1; also elsewhere on the board
/Protected GPIOs/OUT2: DZ5.1 (K), Q5.3 (D), R155.2, R157.1; also elsewhere on the board

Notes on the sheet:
Protected, 1A Open drain outputs

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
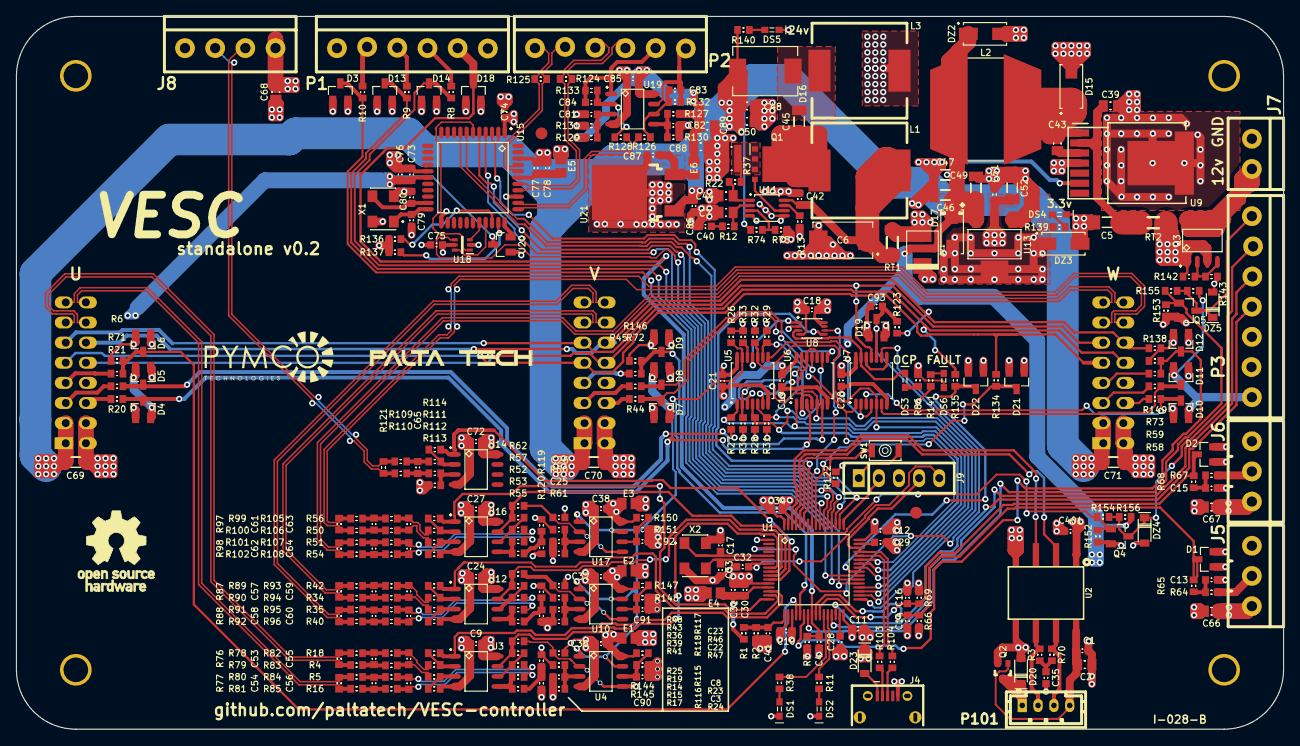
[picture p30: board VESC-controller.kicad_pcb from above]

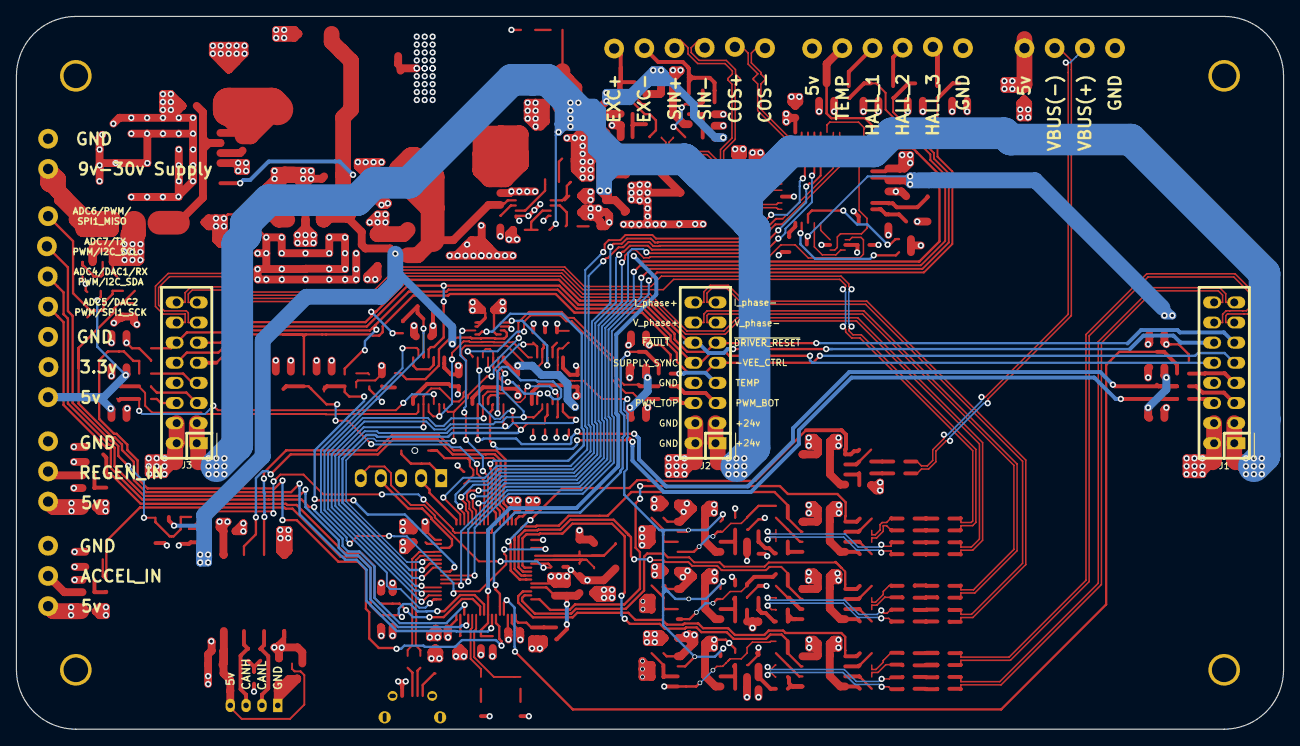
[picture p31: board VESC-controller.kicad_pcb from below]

Board: 4 copper layers, 160.0 x 90.0 mm, 336 parts (3 on the bottom side), 217 nets.

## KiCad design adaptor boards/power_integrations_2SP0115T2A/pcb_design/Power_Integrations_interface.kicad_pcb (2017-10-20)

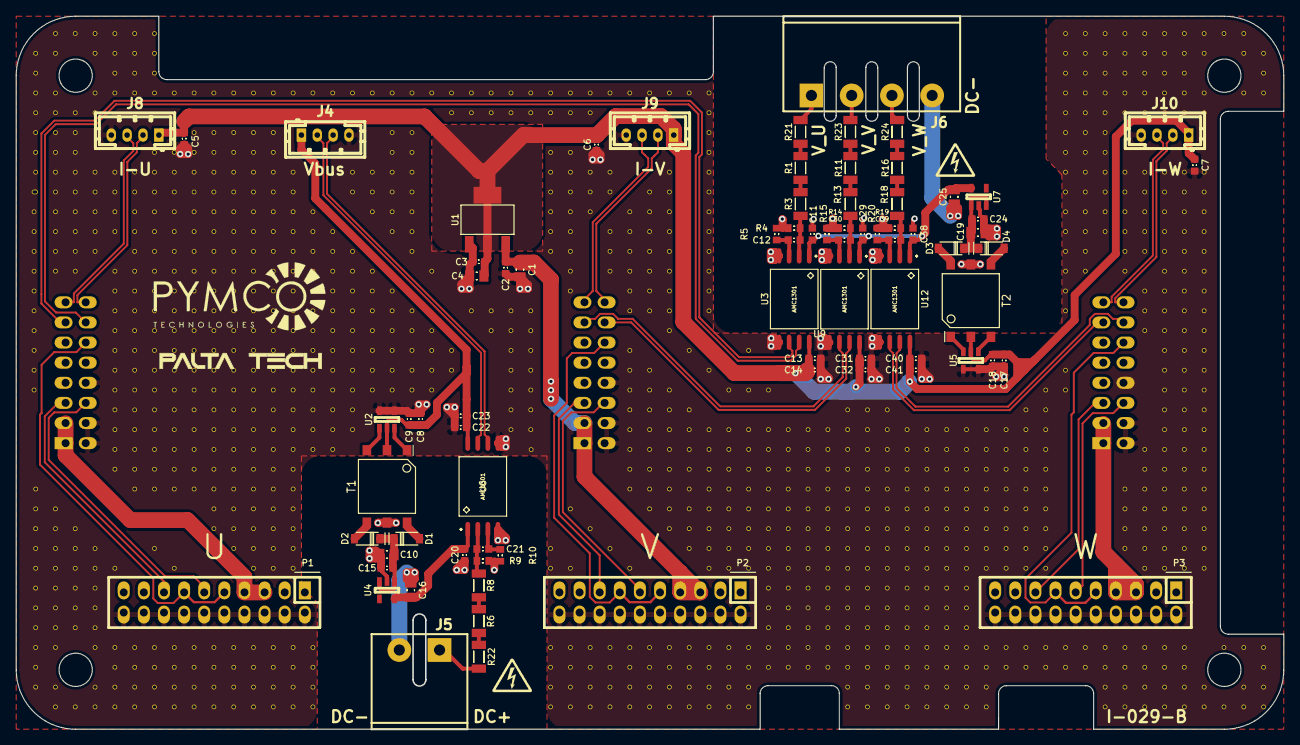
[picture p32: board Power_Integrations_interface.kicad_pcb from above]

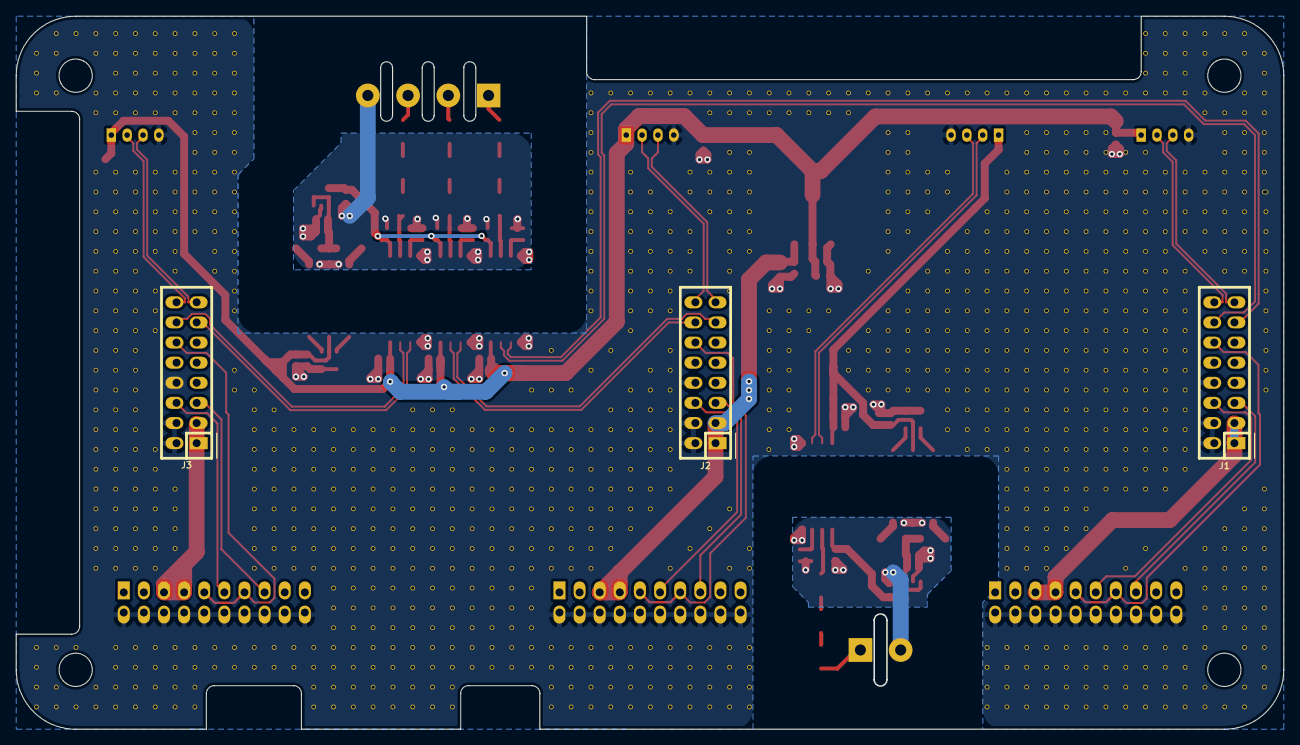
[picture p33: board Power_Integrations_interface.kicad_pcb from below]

Board: 2 copper layers, 160.0 x 90.0 mm, 1122 parts (3 on the bottom side), 63 nets.

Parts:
C1, C4, C10, C16, C19, C25: 22uF; CAPC2012X70
C2, C3, C5, C6, C7, C9, C11, C13, C15, C18, C20, C22, C24, C29, C31, C38, C40: 100nF; CAPC1608X55
C8, C14, C17, C23, C32, C41: 2.2uF; CAPC1608X55
C12, C21, C30, C39: 330pF; CAPC1608X55
D1, D2, D3, D4: MBR0520; SOD-123
J1: GATE_DRIVER_CONN_U; CONN-100MIL-M-2x8
J2: GATE_DRIVER_CONN_V; CONN-100MIL-M-2x8
J3: GATE_DRIVER_CONN_W; CONN-100MIL-M-2x8
J4: VBUS; b4b-ph-kl
J5: CONN-100MIL-F-1x2; mstba_2,5%2f2-g-5,08
J6: Phoenix 1757268 5.08mm; mstba_2,5%2f4-g-5,08
J8, J9, J10: current sensor; b4b-ph-kl
P1, P2, P3: 2SP0115T_conector; CONN-100MIL-F-2x10
R1, R3, R6, R8, R11, R13, R16, R18, R21, R22, R23, R24: 500k; RESC3216X60
R4, R5, R9, R10, R14, R15, R19, R20: 1k; RESC1608X50
T1, T2: TRANS-2CT; WURTH-760390014
U1: LM1117IMP-v.v; SOT-223
U2, U5: SN6501DBV; SOT-23-5
U3, U6, U9, U12: AMC1301; SOIC127P1032X265-8
U4, U7: TPS76350; SOT-23-5
V1_2, V1_3, V1_3#2, V1_4, V1_4#2, V1_5, V1_5#2, V1_6, V1_6#2, V1_7, V1_7#2, V1_7#3, V1_8, V1_8#2, V1_8#3, V1_8#4, V1_9, V1_9#2, V1_9#3, V1_24, V1_25, V1_26, V1_27, V1_28, V1_29, V1_30, V1_31, V1_32, V1_33, V1_34, V2_1, V2_2, V2_4, V2_5, V2_6, V2_7, V2_8, V2_11, V2_11#2, V2_12, V2_12#2, V2_25, V2_26, V2_27, V2_28, V2_29, V2_30, V2_31, V2_32, V2_34, V2_35, V3_1, V3_5, V3_6, V3_7, V3_10, V3_10#2, V3_11, V3_12, V3_12#2, V3_26, V3_27, V3_28, V3_29, V3_29#2, V3_30, V3_30#2, V3_31, V3_31#2, V3_35, V4_1, V4_2, V4_4, V4_5, V4_9, V4_9#2, V4_10, V4_10#2, V4_10#3, V4_11, V4_12, V4_27, V4_28, V4_34, V4_34#2, V4_35, V5_1, V5_2, V5_3, V5_4, V5_8, V5_9, V5_10, V5_11, V5_28, V5_34, V5_34#2, V5_34#3, V5_35, V6_1, V6_2, V6_3, V6_4, V6_8, V6_9, V6_10, V6_12, V6_12#2, V6_13, V6_13#2, V6_14, V6_14#2, V6_15, V6_15#2, V6_16, V6_16#2, V6_17, V6_17#2, V6_17#3, V6_17#4, V6_17#5, V6_17#6, V6_18, V6_18#2, V6_19, V6_19#2, V6_20, V6_20#2, V6_21, V6_21#2, V6_22, V6_22#2, V6_23, V6_23#2, V6_24, V6_34, V6_34#2, V6_34#3, V6_35, V7_1, V7_2, V7_3, V7_7, V7_8, V7_9, V7_11, V7_11#2, V7_12, V7_13, V7_14, V7_15, V7_16, V7_17, V7_17#2, V7_17#3, V7_18, V7_19, V7_20, V7_21, V7_22, V7_23, V7_24, V7_27, V7_34, V7_34#2, V7_34#3, V7_35, V8_8, V8_10, V8_10#2, V8_10#3, V8_11, V8_12, V8_13, V8_14, V8_15, V8_16, V8_17, V8_17#2, V8_17#3, V8_18, V8_19, V8_20, V8_21, V8_22, V8_23, V8_24, V8_28, V8_34, V8_34#2, V8_34#3, V8_35, V9_9, V9_9#2, V9_9#3, V9_9#4, V9_10, V9_11, V9_12, V9_13, V9_14, V9_15, V9_16, V9_17, V9_17#2, V9_17#3, V9_18, V9_19, V9_20, V9_21, V9_22, V9_23, V9_24, V9_34, V9_34#2, V9_34#3, V9_35, V10_8, V10_8#2, V10_9, V10_9#2, V10_10, V10_11, V10_12, V10_13, V10_14, V10_15, V10_16, V10_17, V10_17#2, V10_17#3, V10_18, V10_19, V10_20, V10_21, V10_22, V10_23, V10_24, V10_25, V10_26, V10_34, V10_34#2, V10_34#3, V10_35, V11_8, V11_8#2, V11_9, V11_9#2, V11_10, V11_11, V11_12, V11_13, V11_14, V11_15, V11_16, V11_17, V11_17#2, V11_17#3, V11_18, V11_19, V11_20, V11_21, V11_22, V11_23, V11_24, V11_25, V11_26, V11_27, V11_34, V11_34#2, V11_34#3, V11_35, V12_8, V12_8#2, V12_9, V12_9#2, V12_10, V12_11, V12_12, V12_13, V12_14, V12_15, V12_16, V12_17, V12_17#2, V12_17#3, V12_18, V12_19, V12_20, V12_21, V12_22, V12_23, V12_24, V12_25, V12_26, V12_27, V12_28, V12_34, V12_34#2, V12_34#3, V12_35, V13_8, V13_8#2, V13_9, V13_9#2, V13_10, V13_11, V13_12, V13_13, V13_14, V13_15, V13_16, V13_17, V13_17#2, V13_17#3, V13_18, V13_19, V13_20, V13_21, V13_22, V13_23, V13_24, V13_25, V13_26, V13_27, V13_28, V13_34, V13_34#2, V13_34#3, V13_35, V14_8, V14_9, V14_10, V14_11, V14_12, V14_13, V14_14, V14_15, V14_16, V14_17, V14_17#2, V14_17#3, V14_18, V14_19, V14_20, V14_21, V14_22, V14_23, V14_24, V14_25, V14_26, V14_27, V14_28, V14_34, V14_34#2, V14_34#3, V14_35, V15_10, V15_11, V15_12, V15_13, V15_14, V15_15, V15_16, V15_17, V15_17#2, V15_18, V15_19, V15_20, V15_21, V15_22, V15_34, V15_34#2, V15_34#3, V15_35, V16_11, V16_12, V16_13, V16_14, V16_15, V16_16, V16_17, V16_17#2, V16_18, V16_19, V16_19#2, V16_20, V16_20#2, V16_21, V16_21#2, V16_22, V17_8, V17_9, V17_12, V17_13, V17_14, V17_15, V17_16, V17_17, V17_17#2, V17_18, V18_8, V18_9, V18_10, V18_13, V18_14, V18_15, V18_16, V18_17, V18_17#2, V18_18, V18_18#2, V19_6, V19_7, V19_8, V19_9, V19_10, V19_11, V19_14, V19_15, V19_16, V19_17, V19_17#2, V19_18, V19_18#2, V20_6, V20_7, V20_8, V20_9, V20_10, V20_11, V20_12, V20_15, V20_16, V20_17, V20_17#2, V20_18, V20_18#2, V21_13, V21_16, V21_17, V21_17#2, V21_18, V21_18#2, V22_5, V22_17, V22_17#2, V22_18, V23_5, V23_15, V24_5, V24_15, V24_16, V25_5, V25_15, V25_16, V25_17, V25_18, V25_19, V25_20, V25_20#2, V26_5, V26_5#2, V26_15, V26_16, V26_17, V26_18, V26_19, V26_20, V26_20#2, V26_20#3, V27_5, V27_5#2, V27_7, V27_7#2, V27_8, V27_9, V27_9#2, V27_10, V27_10#2, V27_27, V27_28, V27_34, V27_34#2, V27_34#3, V27_34#4, V27_35, V28_9, V28_9#2, V28_10, V28_10#2, V28_11, V28_11#2, V28_12, V28_12#2, V28_25, V28_28, V28_34, V28_34#2, V28_34#3, V28_34#4, V28_35, V29_9, V29_9#2, V29_9#3, V29_9#4, V29_26, V29_34, V29_34#2, V29_34#3, V29_34#4, V29_35, V30_11, V30_12, V30_12#2, V30_27, V30_34, V30_34#2, V30_34#3, V30_34#4, V30_35, V31_10, V31_11, V31_12, V31_12#2, V31_12#3, V31_12#4, V31_24, V31_28, V31_34, V31_34#2, V31_34#3, V31_34#4, V31_35, V32_9, V32_10, V32_11, V32_12, V32_13, V32_14, V32_15, V32_18, V32_18#2, V32_19, V32_19#2, V32_19#3, V32_20, V32_20#2, V32_21, V32_21#2, V32_22, V32_22#2, V32_23, V32_23#2, V32_24, V32_25, V32_34, V32_34#2, V32_34#3, V32_34#4, V32_34#5, V32_35, V33_8, V33_8#2, V33_8#3, V33_9, V33_9#2, V33_9#3, V33_10, V33_10#2, V33_11, V33_11#2, V33_12, V33_12#2, V33_13, V33_13#2, V33_14, V33_14#2, V33_15, V33_15#2, V33_16, V33_16#2, V33_19, V33_20, V33_21, V33_22, V33_23, V33_24, V33_25, V33_26, V33_34, V33_34#2, V33_34#3, V33_34#4, V33_34#5, V33_35, V34_17, V34_20, V34_21, V34_22, V34_23, V34_24, V34_25, V34_26, V34_27, V34_34, V34_34#2, V34_34#3, V34_34#4, V34_34#5, V34_35, V35_4, V35_18, V35_21, V35_22, V35_23, V35_24, V35_25, V35_26, V35_27, V35_28, V35_34, V35_34#2, V35_34#3, V35_34#4, V35_34#5, V35_35, V36_19, V36_19#2, V36_21, V36_22, V36_23, V36_24, V36_25, V36_26, V36_27, V36_28, V36_34, V36_34#2, V36_34#3, V36_34#4, V36_34#5, V36_35, V37_19, V37_21, V37_22, V37_23, V37_24, V37_25, V37_26, V37_27, V37_28, V37_34, V37_34#2, V37_34#3, V37_34#4, V37_34#5, V37_35, V38_19, V38_21, V38_22, V38_23, V38_24, V38_25, V38_26, V38_27, V38_28, V38_34, V38_34#2, V38_34#3, V39_21, V39_22, V39_23, V39_24, V39_25, V39_26, V39_27, V39_28, V39_29, V39_29#2, V39_30, V39_30#2, V39_31, V39_31#2, V39_32, V39_32#2, V39_33, V40_21, V40_22, V40_23, V40_24, V40_25, V40_26, V40_27, V40_28, V40_29, V40_30, V40_31, V40_32, V40_33, V41_21, V41_22, V41_23, V41_24, V41_25, V41_26, V41_27, V41_28, V41_29, V41_30, V41_31, V41_32, V41_33, V42_20, V42_21, V42_22, V42_23, V42_24, V42_25, V42_26, V42_27, V42_28, V42_29, V42_30, V42_31, V42_32, V42_33, V42_34, V42_35, V43_20, V43_21, V43_22, V43_23, V43_24, V43_25, V43_26, V43_27, V43_28, V43_29, V43_30, V43_31, V43_32, V43_33, V43_34, V43_35, V44_20, V44_21, V44_22, V44_23, V44_24, V44_25, V44_26, V44_27, V44_28, V44_29, V44_30, V44_31, V44_32, V44_33, V44_34, V44_35, V45_21, V45_22, V45_23, V45_24, V45_25, V45_26, V45_27, V45_28, V45_29, V45_30, V45_31, V45_32, V45_33, V45_34, V45_35, V46_21, V46_22, V46_23, V46_24, V46_25, V46_26, V46_27, V46_28, V46_29, V46_30, V46_31, V46_32, V46_33, V46_34, V46_35, V47_21, V47_22, V47_23, V47_24, V47_25, V47_26, V47_27, V47_28, V47_29, V47_30, V47_30#2, V47_31, V47_31#2, V47_32, V47_32#2, V47_33, V47_34, V47_35, V48_21, V48_22, V48_23, V48_24, V48_25, V48_26, V48_27, V48_28, V48_28#2, V48_34, V48_35, V49_21, V49_22, V49_23, V49_24, V49_25, V49_26, V49_27, V49_28, V49_28#2, V49_34, V49_35, V50_21, V50_22, V50_23, V50_24, V50_25, V50_26, V50_27, V50_28, V50_28#2, V51_20, V51_21, V51_22, V51_23, V51_24, V51_25, V51_26, V51_27, V51_28, V51_28#2, V52_19, V52_20, V52_21, V52_22, V52_23, V52_24, V52_25, V52_26, V52_27, V52_28, V52_28#2, V53_1, V53_2, V53_3, V53_4, V53_4#2, V53_10, V53_11, V53_12, V53_13, V53_14, V53_15, V53_18, V53_19, V54_1, V54_2, V54_3, V54_4, V54_4#2, V54_12, V54_12#2, V55_1, V55_2, V55_3, V55_4, V55_4#2, V55_10, V55_11, V55_34, V55_35, V56_1, V56_2, V56_3, V56_4, V56_8, V56_9, V56_10, V56_11, V56_12, V56_12#2, V56_24, V56_25, V56_26, V56_27, V56_34, V56_35, V57_1, V57_2, V57_3, V57_4, V57_5, V57_6, V57_6#2, V57_7, V57_7#2, V57_8, V57_9, V57_10, V57_11, V57_12, V57_24, V57_24#2, V57_25, V57_25#2, V57_26, V57_27, V57_28, V57_34, V57_35, V58_1, V58_2, V58_3, V58_4, V58_5, V58_6, V58_6#2, V58_6#3, V58_7, V58_7#2, V58_7#3, V58_8, V58_9, V58_10, V58_11, V58_12, V58_13, V58_14, V58_14#2, V58_15, V58_15#2, V58_16, V58_16#2, V58_17, V58_18, V58_19, V58_20, V58_21, V58_22, V58_23, V58_24, V58_25, V58_26, V58_27, V58_28, V58_34, V58_35, V59_1, V59_2, V59_3, V59_4, V59_5, V59_6, V59_6#2, V59_7, V59_7#2, V59_8, V59_9, V59_10, V59_11, V59_12, V59_13, V59_14, V59_15, V59_16, V59_17, V59_18, V59_19, V59_20, V59_21, V59_22, V59_23, V59_24, V59_25, V59_26, V59_27, V59_28, V59_34, V59_35, V60_1, V60_2, V60_4, V60_5, V60_6, V60_8, V60_9, V60_10, V60_11, V60_12, V60_13, V60_14, V60_15, V60_16, V60_17, V60_18, V60_19, V60_20, V60_21, V60_22, V60_23, V60_24, V60_25, V60_26, V60_27, V60_28, V60_34, V60_35, V61_1, V61_32, V61_35, V62_1, V62_2, V62_4, V62_32, V62_34, V62_35, V63_2, V63_3, V63_4, V63_32, V63_33, V63_34, V63_35: AUTO_VIA; VIA_MATRIX

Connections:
15v_U: J1.1, J1.3, P1.5, P1.7
15v_V: C1.1, C2.1, J2.1, J2.3, P2.5, P2.7, U1.3
15v_W: J3.1, J3.3, P3.5, P3.7
+5: C3.1, C4.1, C5.1, C6.1, C7.1, C13.1, C14.1, C17.1, C18.1, C31.1, C32.1, C40.1, C41.1, J8.1, J9.1, J10.1, T2.2, U1.2, U1.4, U3.8, U5.2, U9.8, U12.8
+5A: C11.2, C25.1, C29.2, C38.2, U3.1, U7.5, U9.1, U12.1
/I_phase_U+: J1.16, J8.2
/I_phase_U-: J1.15, J8.3
/I_phase_V+: J2.16, J9.2
/I_phase_V-: J2.15, J9.3
/I_phase_W+: J3.16, J10.2
/I_phase_W-: J3.15, J10.3
/V_BUS/GND2: C10.2, C15.2, C16.2, C20.1, J5.2, R9.2, R10.1, T1.5, U4.2, U6.4
/V_BUS/VDD1: C8.1, C9.1, C22.1, C23.1, J4.1, T1.2, U2.2, U6.8
/V_BUS/VDD2: C16.1, C20.2, U4.5, U6.1
/V_BUS/VIN+: C21.1, R8.1, R9.1, U6.2
/V_BUS/VIN-: C21.2, R10.2, U6.3
/V_BUS/Vin+: J5.1, R22.2
/V_phase_U/VIN+: C12.1, R3.1, R4.1, U3.2
/V_phase_U/VIN-: C12.2, R5.2, U3.3
/V_phase_U/Vin+: J6.1, R21.2
/V_phase_U/Vout+: J1.14, U3.7
/V_phase_U/Vout-: J1.13, U3.6
/V_phase_V/VIN+: C30.1, R13.1, R14.1, U9.2
/V_phase_V/VIN-: C30.2, R15.2, U9.3
/V_phase_V/Vin+: J6.2, R23.2
/V_phase_V/Vout+: J2.14, U9.7
/V_phase_V/Vout-: J2.13, U9.6
/V_phase_W/VIN+: C39.1, R18.1, R19.1, U12.2
/V_phase_W/VIN-: C39.2, R20.2, U12.3
/V_phase_W/Vin+: J6.3, R24.2
/V_phase_W/Vout+: J3.14, U12.7
/V_phase_W/Vout-: J3.13, U12.6
/vbus+: J4.2, U6.7
/vbus-: J4.3, U6.6
GND: C1.2, C2.2, C3.2, C4.2, C5.2, C6.2, C7.2, C8.2, C9.2, C13.2, C14.2, C17.2, C18.2, C22.2, C23.2, C31.2, C32.2, C40.2, C41.2, J1.2, J1.4, J1.8, J2.2, J2.4, J2.8, J3.2, J3.4, J3.8, J4.4, J8.4, J9.4, J10.4, P1.2, P1.4, P1.6, P1.8, P1.10, P1.12, P1.14, P1.16, P1.18, P1.20, P2.2, P2.4, P2.6, P2.8, P2.10, P2.12, P2.14, P2.16, P2.18, P2.20, P3.2, P3.4, P3.6, P3.8, P3.10, P3.12, P3.14, P3.16, P3.18, P3.20, U1.1, U2.4, U2.5, U3.5, U5.4, U5.5, U6.5, U9.5, U12.5, V1_2.1, V1_3.1, V1_3#2.1, V1_4.1, V1_4#2.1, V1_5.1, V1_5#2.1, V1_6.1, V1_6#2.1, V1_7.1, V1_7#2.1, V1_7#3.1, V1_8.1, V1_8#2.1, V1_8#3.1, V1_8#4.1, V1_9.1, V1_9#2.1, V1_9#3.1, V1_24.1, V1_25.1, V1_26.1, V1_27.1, V1_28.1, V1_29.1, V1_30.1, V1_31.1, V1_32.1, V1_33.1, V1_34.1, V2_1.1, V2_2.1, V2_4.1, V2_5.1, V2_6.1, V2_7.1, V2_8.1, V2_11.1, V2_11#2.1, V2_12.1, V2_12#2.1, V2_25.1, V2_26.1, V2_27.1, V2_28.1, V2_29.1, V2_30.1, V2_31.1, V2_32.1, V2_34.1, V2_35.1, V3_1.1, V3_5.1, V3_6.1, V3_7.1, V3_10.1, V3_10#2.1, V3_11.1, V3_12.1, V3_12#2.1, V3_26.1, V3_27.1, V3_28.1, V3_29.1, V3_29#2.1, V3_30.1, V3_30#2.1, V3_31.1, V3_31#2.1, V3_35.1, V4_1.1, V4_2.1, V4_4.1, V4_5.1, V4_9.1, V4_9#2.1, V4_10.1, V4_10#2.1, V4_10#3.1, V4_11.1, V4_12.1, V4_27.1, V4_28.1, V4_34.1, V4_34#2.1, V4_35.1, V5_1.1, V5_2.1, V5_3.1, V5_4.1, V5_8.1, V5_9.1, V5_10.1, V5_11.1, V5_28.1, V5_34.1, V5_34#2.1, V5_34#3.1, V5_35.1, V6_1.1, V6_2.1, V6_3.1, V6_4.1, V6_8.1, V6_9.1, V6_10.1, V6_12.1, V6_12#2.1, V6_13.1, V6_13#2.1, V6_14.1, V6_14#2.1, V6_15.1, V6_15#2.1, V6_16.1, V6_16#2.1, V6_17.1, V6_17#2.1, V6_17#3.1, V6_17#4.1, V6_17#5.1, V6_17#6.1, V6_18.1, V6_18#2.1, V6_19.1, V6_19#2.1, V6_20.1, V6_20#2.1, V6_21.1, V6_21#2.1, V6_22.1, V6_22#2.1, V6_23.1, V6_23#2.1, V6_24.1, V6_34.1, V6_34#2.1, V6_34#3.1, V6_35.1, V7_1.1, V7_2.1, V7_3.1, V7_7.1, V7_8.1, V7_9.1, V7_11.1, V7_11#2.1, V7_12.1, V7_13.1, V7_14.1, V7_15.1, V7_16.1, V7_17.1, V7_17#2.1, V7_17#3.1, V7_18.1, V7_19.1, V7_20.1, V7_21.1, V7_22.1, V7_23.1, V7_24.1, V7_27.1, V7_34.1, V7_34#2.1, V7_34#3.1, V7_35.1, V8_8.1, V8_10.1, V8_10#2.1, V8_10#3.1, V8_11.1, V8_12.1, V8_13.1, V8_14.1, V8_15.1, V8_16.1, V8_17.1, V8_17#2.1, V8_17#3.1, V8_18.1, V8_19.1, V8_20.1, V8_21.1, V8_22.1, V8_23.1, V8_24.1, V8_28.1, V8_34.1, V8_34#2.1, V8_34#3.1, V8_35.1, V9_9.1, V9_9#2.1, V9_9#3.1, V9_9#4.1, V9_10.1, V9_11.1, V9_12.1, V9_13.1, V9_14.1, V9_15.1, V9_16.1, V9_17.1, V9_17#2.1, V9_17#3.1, V9_18.1, V9_19.1, V9_20.1, V9_21.1, V9_22.1, V9_23.1, V9_24.1, V9_34.1, V9_34#2.1, V9_34#3.1, V9_35.1, V10_8.1, V10_8#2.1, V10_9.1, V10_9#2.1, V10_10.1, V10_11.1, V10_12.1, V10_13.1, V10_14.1, V10_15.1, V10_16.1, V10_17.1, V10_17#2.1, V10_17#3.1, V10_18.1, V10_19.1, V10_20.1, V10_21.1, V10_22.1, V10_23.1, V10_24.1, V10_25.1, V10_26.1, V10_34.1, V10_34#2.1, V10_34#3.1, V10_35.1, V11_8.1, V11_8#2.1, V11_9.1, V11_9#2.1, V11_10.1, V11_11.1, V11_12.1, V11_13.1, V11_14.1, V11_15.1, V11_16.1, V11_17.1, V11_17#2.1, V11_17#3.1, V11_18.1, V11_19.1, V11_20.1, V11_21.1, V11_22.1, V11_23.1, V11_24.1, V11_25.1, V11_26.1, V11_27.1, V11_34.1, V11_34#2.1, V11_34#3.1, V11_35.1, V12_8.1, V12_8#2.1, V12_9.1, V12_9#2.1, V12_10.1, V12_11.1, V12_12.1, V12_13.1, V12_14.1, V12_15.1, V12_16.1, V12_17.1, V12_17#2.1, V12_17#3.1, V12_18.1, V12_19.1, V12_20.1, V12_21.1, V12_22.1, V12_23.1, V12_24.1, V12_25.1, V12_26.1, V12_27.1, V12_28.1, V12_34.1, V12_34#2.1, V12_34#3.1, V12_35.1, V13_8.1, V13_8#2.1, V13_9.1, V13_9#2.1, V13_10.1, V13_11.1, V13_12.1, V13_13.1, V13_14.1, V13_15.1, V13_16.1, V13_17.1, V13_17#2.1, V13_17#3.1, V13_18.1, V13_19.1, V13_20.1, V13_21.1, V13_22.1, V13_23.1, V13_24.1, V13_25.1, V13_26.1, V13_27.1, V13_28.1, V13_34.1, V13_34#2.1, V13_34#3.1, V13_35.1, V14_8.1, V14_9.1, V14_10.1, V14_11.1, V14_12.1, V14_13.1, V14_14.1, V14_15.1, V14_16.1, V14_17.1, V14_17#2.1, V14_17#3.1, V14_18.1, V14_19.1, V14_20.1, V14_21.1, V14_22.1, V14_23.1, V14_24.1, V14_25.1, V14_26.1, V14_27.1, V14_28.1, V14_34.1, V14_34#2.1, V14_34#3.1, V14_35.1, V15_10.1, V15_11.1, V15_12.1, V15_13.1, V15_14.1, V15_15.1, V15_16.1, V15_17.1, V15_17#2.1, V15_18.1, V15_19.1, V15_20.1, V15_21.1, V15_22.1, V15_34.1, V15_34#2.1, V15_34#3.1, V15_35.1, V16_11.1, V16_12.1, V16_13.1, V16_14.1, V16_15.1, V16_16.1, V16_17.1, V16_17#2.1, V16_18.1, V16_19.1, V16_19#2.1, V16_20.1, V16_20#2.1, V16_21.1, V16_21#2.1, V16_22.1, V17_8.1, V17_9.1, V17_12.1, V17_13.1, V17_14.1, V17_15.1, V17_16.1, V17_17.1, V17_17#2.1, V17_18.1, V18_8.1, V18_9.1, V18_10.1, V18_13.1, V18_14.1, V18_15.1, V18_16.1, V18_17.1, V18_17#2.1, V18_18.1, V18_18#2.1, V19_6.1, V19_7.1, V19_8.1, V19_9.1, V19_10.1, V19_11.1, V19_14.1, V19_15.1, V19_16.1, V19_17.1, V19_17#2.1, V19_18.1, V19_18#2.1, V20_6.1, V20_7.1, V20_8.1, V20_9.1, V20_10.1, V20_11.1, V20_12.1, V20_15.1, V20_16.1, V20_17.1, V20_17#2.1, V20_18.1, V20_18#2.1, V21_13.1, V21_16.1, V21_17.1, V21_17#2.1, V21_18.1, V21_18#2.1, V22_5.1, V22_17.1, V22_17#2.1, V22_18.1, V23_5.1, V23_15.1, V24_5.1, V24_15.1, V24_16.1, V25_5.1, V25_15.1, V25_16.1, V25_17.1, V25_18.1, V25_19.1, V25_20.1, V25_20#2.1, V26_5.1, V26_5#2.1, V26_15.1, V26_16.1, V26_17.1, V26_18.1, V26_19.1, V26_20.1, V26_20#2.1, V26_20#3.1, V27_5.1, V27_5#2.1, V27_7.1, V27_7#2.1, V27_8.1, V27_9.1, V27_9#2.1, V27_10.1, V27_10#2.1, V27_27.1, V27_28.1, V27_34.1, V27_34#2.1, V27_34#3.1, V27_34#4.1, V27_35.1, V28_9.1, V28_9#2.1, V28_10.1, V28_10#2.1, V28_11.1, V28_11#2.1, V28_12.1, V28_12#2.1, V28_25.1, V28_28.1, V28_34.1, V28_34#2.1, V28_34#3.1, V28_34#4.1, V28_35.1, V29_9.1, V29_9#2.1, V29_9#3.1, V29_9#4.1, V29_26.1, V29_34.1, V29_34#2.1, V29_34#3.1, V29_34#4.1, V29_35.1, V30_11.1, V30_12.1, V30_12#2.1, V30_27.1, V30_34.1, V30_34#2.1, V30_34#3.1, V30_34#4.1, V30_35.1, V31_10.1, V31_11.1, V31_12.1, V31_12#2.1, V31_12#3.1, V31_12#4.1, V31_24.1, V31_28.1, V31_34.1, V31_34#2.1, V31_34#3.1, V31_34#4.1, V31_35.1, V32_9.1, V32_10.1, V32_11.1, V32_12.1, V32_13.1, V32_14.1, V32_15.1, V32_18.1, V32_18#2.1, V32_19.1, V32_19#2.1, V32_19#3.1, V32_20.1, V32_20#2.1, V32_21.1, V32_21#2.1, V32_22.1, V32_22#2.1, V32_23.1, V32_23#2.1, V32_24.1, V32_25.1, V32_34.1, V32_34#2.1, V32_34#3.1, V32_34#4.1, V32_34#5.1, V32_35.1, V33_8.1, V33_8#2.1, V33_8#3.1, V33_9.1, V33_9#2.1, V33_9#3.1, V33_10.1, V33_10#2.1, V33_11.1, V33_11#2.1, V33_12.1, V33_12#2.1, V33_13.1, V33_13#2.1, V33_14.1, V33_14#2.1, V33_15.1, V33_15#2.1, V33_16.1, V33_16#2.1, V33_19.1, V33_20.1, V33_21.1, V33_22.1, V33_23.1, V33_24.1, V33_25.1, V33_26.1, V33_34.1, V33_34#2.1, V33_34#3.1, V33_34#4.1, V33_34#5.1, V33_35.1, V34_17.1, V34_20.1, V34_21.1, V34_22.1, V34_23.1, V34_24.1, V34_25.1, V34_26.1, V34_27.1, V34_34.1, V34_34#2.1, V34_34#3.1, V34_34#4.1, V34_34#5.1, V34_35.1, V35_4.1, V35_18.1, V35_21.1, V35_22.1, V35_23.1, V35_24.1, V35_25.1, V35_26.1, V35_27.1, V35_28.1, V35_34.1, V35_34#2.1, V35_34#3.1, V35_34#4.1, V35_34#5.1, V35_35.1, V36_19.1, V36_19#2.1, V36_21.1, V36_22.1, V36_23.1, V36_24.1, V36_25.1, V36_26.1, V36_27.1, V36_28.1, V36_34.1, V36_34#2.1, V36_34#3.1, V36_34#4.1, V36_34#5.1, V36_35.1, V37_19.1, V37_21.1, V37_22.1, V37_23.1, V37_24.1, V37_25.1, V37_26.1, V37_27.1, V37_28.1, V37_34.1, V37_34#2.1, V37_34#3.1, V37_34#4.1, V37_34#5.1, V37_35.1, V38_19.1, V38_21.1, V38_22.1, V38_23.1, V38_24.1, V38_25.1, V38_26.1, V38_27.1, V38_28.1, V38_34.1, V38_34#2.1, V38_34#3.1, V39_21.1, V39_22.1, V39_23.1, V39_24.1, V39_25.1, V39_26.1, V39_27.1, V39_28.1, V39_29.1, V39_29#2.1, V39_30.1, V39_30#2.1, V39_31.1, V39_31#2.1, V39_32.1, V39_32#2.1, V39_33.1, V40_21.1, V40_22.1, V40_23.1, V40_24.1, V40_25.1, V40_26.1, V40_27.1, V40_28.1, V40_29.1, V40_30.1, V40_31.1, V40_32.1, V40_33.1, V41_21.1, V41_22.1, V41_23.1, V41_24.1, V41_25.1, V41_26.1, V41_27.1, V41_28.1, V41_29.1, V41_30.1, V41_31.1, V41_32.1, V41_33.1, V42_20.1, V42_21.1, V42_22.1, V42_23.1, V42_24.1, V42_25.1, V42_26.1, V42_27.1, V42_28.1, V42_29.1, V42_30.1, V42_31.1, V42_32.1, V42_33.1, V42_34.1, V42_35.1, V43_20.1, V43_21.1, V43_22.1, V43_23.1, V43_24.1, V43_25.1, V43_26.1, V43_27.1, V43_28.1, V43_29.1, V43_30.1, V43_31.1, V43_32.1, V43_33.1, V43_34.1, V43_35.1, V44_20.1, V44_21.1, V44_22.1, V44_23.1, V44_24.1, V44_25.1, V44_26.1, V44_27.1, V44_28.1, V44_29.1, V44_30.1, V44_31.1, V44_32.1, V44_33.1, V44_34.1, V44_35.1, V45_21.1, V45_22.1, V45_23.1, V45_24.1, V45_25.1, V45_26.1, V45_27.1, V45_28.1, V45_29.1, V45_30.1, V45_31.1, V45_32.1, V45_33.1, V45_34.1, V45_35.1, V46_21.1, V46_22.1, V46_23.1, V46_24.1, V46_25.1, V46_26.1, V46_27.1, V46_28.1, V46_29.1, V46_30.1, V46_31.1, V46_32.1, V46_33.1, V46_34.1, V46_35.1, V47_21.1, V47_22.1, V47_23.1, V47_24.1, V47_25.1, V47_26.1, V47_27.1, V47_28.1, V47_29.1, V47_30.1, V47_30#2.1, V47_31.1, V47_31#2.1, V47_32.1, V47_32#2.1, V47_33.1, V47_34.1, V47_35.1, V48_21.1, V48_22.1, V48_23.1, V48_24.1, V48_25.1, V48_26.1, V48_27.1, V48_28.1, V48_28#2.1, V48_34.1, V48_35.1, V49_21.1, V49_22.1, V49_23.1, V49_24.1, V49_25.1, V49_26.1, V49_27.1, V49_28.1, V49_28#2.1, V49_34.1, V49_35.1, V50_21.1, V50_22.1, V50_23.1, V50_24.1, V50_25.1, V50_26.1, V50_27.1, V50_28.1, V50_28#2.1, V51_20.1, V51_21.1, V51_22.1, V51_23.1, V51_24.1, V51_25.1, V51_26.1, V51_27.1, V51_28.1, V51_28#2.1, V52_19.1, V52_20.1, V52_21.1, V52_22.1, V52_23.1, V52_24.1, V52_25.1, V52_26.1, V52_27.1, V52_28.1, V52_28#2.1, V53_1.1, V53_2.1, V53_3.1, V53_4.1, V53_4#2.1, V53_10.1, V53_11.1, V53_12.1, V53_13.1, V53_14.1, V53_15.1, V53_18.1, V53_19.1, V54_1.1, V54_2.1, V54_3.1, V54_4.1, V54_4#2.1, V54_12.1, V54_12#2.1, V55_1.1, V55_2.1, V55_3.1, V55_4.1, V55_4#2.1, V55_10.1, V55_11.1, V55_34.1, V55_35.1, V56_1.1, V56_2.1, V56_3.1, V56_4.1, V56_8.1, V56_9.1, V56_10.1, V56_11.1, V56_12.1, V56_12#2.1, V56_24.1, V56_25.1, V56_26.1, V56_27.1, V56_34.1, V56_35.1, V57_1.1, V57_2.1, V57_3.1, V57_4.1, V57_5.1, V57_6.1, V57_6#2.1, V57_7.1, V57_7#2.1, V57_8.1, V57_9.1, V57_10.1, V57_11.1, V57_12.1, V57_24.1, V57_24#2.1, V57_25.1, V57_25#2.1, V57_26.1, V57_27.1, V57_28.1, V57_34.1, V57_35.1, V58_1.1, V58_2.1, V58_3.1, V58_4.1, V58_5.1, V58_6.1, V58_6#2.1, V58_6#3.1, V58_7.1, V58_7#2.1, V58_7#3.1, V58_8.1, V58_9.1, V58_10.1, V58_11.1, V58_12.1, V58_13.1, V58_14.1, V58_14#2.1, V58_15.1, V58_15#2.1, V58_16.1, V58_16#2.1, V58_17.1, V58_18.1, V58_19.1, V58_20.1, V58_21.1, V58_22.1, V58_23.1, V58_24.1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
ISOGND: C11.1, C19.2, C24.2, C25.2, C29.1, C38.1, J6.4, R4.2, R5.1, R14.2, R15.1, R19.2, R20.1, T2.5, U3.4, U7.2, U9.4, U12.4
unnamed: C10.1, C15.1, D1.1, D2.1, U4.1, U4.3
unnamed: C19.1, C24.1, D3.1, D4.1, U7.1, U7.3
unnamed: D1.2, T1.6
unnamed: D2.2, T1.4
unnamed: D3.2, T2.6
unnamed: D4.2, T2.4
unnamed: J1.5, P1.15
unnamed: J1.6, P1.11
unnamed: J2.5, P2.15
unnamed: J2.6, P2.11
unnamed: J3.5, P3.15
unnamed: J3.6, P3.11
unnamed: R1.1, R3.2
unnamed: R1.2, R21.1
unnamed: R6.1, R8.2
unnamed: R11.1, R13.2
unnamed: R11.2, R23.1
unnamed: R16.1, R18.2
unnamed: R16.2, R24.1
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

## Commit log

2017-01-23 Added libraries and kicad project
    [VESC-controller.kicad_pcb, VESC-controller.sch]
2017-01-24 Added base VESC 4.xx schematic, added protection features, signal conditioning and pcb form factor
    [CAN.sch, Power.sch, STM32F4 64LQFP.sch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]
2017-01-25 Updated MCU sheet to comply with VESC 6 pinout. Added 5v analog inputs and updated some labels
    [5v to 3.sch, CAN.sch, MCU.sch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]
2017-01-26 Components placement, 3D models, updated some footprints to nominal IPC type
    [5v to 3.sch, CAN.sch, MCU.sch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]
2017-01-26 Added terminal blocks and power supplies
    [5v to 3.sch, CAN.sch, MCU.sch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]
2017-01-27 Added lp filters, fuses, tvs and power symbols
    [CAN.sch, MCU.sch, VESC-controller.kicad_pcb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]
2017-01-27 Added bus voltage conditioning, %v to accel and regen inputs, regulator diode, annotated schematic
    [5v to 3.sch, CAN.sch, MCU.sch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]
2017-01-28 Fixed issue with non-bidirectional phase current measurement. Started routing power supplies. Changed terminal blocks from 5.00mm to 3.81mm pitch
    [5v to 3.sch, CAN.sch, MCU.sch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]
2017-01-29 More layout
    [5v to 3.sch, CAN.sch, MCU.sch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]
2017-01-29 More layout. Changed LED pin. Added placeholder for a resolver IC
    [5v to 3.sch, ABM3B.step, CAN.sch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]
2017-01-30 Added reverse polarity protection on the isolated side of CON connector. Also, more layout
    [5v to 3.sch, CAN.sch, MCU.sch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]
2017-01-31 Resolver routed using push pull buffer
    [5v to 3.sch, CAN.sch, MCU.sch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]
2017-01-31 Resolver routed. Added 12v regulator. The screw terminals were backwards(!). Started clearing up DRC markers.
    [MCU.sch, VESC-controller.kicad_pcb, VESC-controller.sch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]
2017-02-01 Routing complete. Added 3D models. No DRC errors, a few ERC warnings
    [5v to 3.sch, CAN.sch, MCU.sch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]
2017-02-01 Added frequency set resistors for the resolver. Fixed protection mosfet installed backwards. More 3D models
    [B4B-PH-K-S.step, VESC-controller.kicad_pcb, power.sch]
2017-02-02 Moved references
    [VESC-controller.kicad_pcb, VESC-controller.sch]
2017-02-03 Had a missing pullup for the fault signal. Added silkcreens on the bottom
    [VESC-controller.kicad_pcb, _saved_supervisor.sch]
2017-02-05 Silkscreen logos, fixed swapped OCP inputs, added a button to enter bootloader,missing 3d model.
    [5v to 3.sch, B3U_1000P.step, CAN.sch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]
2017-02-06 Files sent to the manufacturer. This is VESC-controller v0.1
    [VESC-controller.kicad_pcb]
2017-02-07 Updated component values according to simulations. 1.5khz for user inputs and 240khz lp pass filters for motor control
    [5v to 3.sch, CAN.sch, VESC-controller.kicad_pcb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]
2017-02-07 Completed some part numbers
    [5v to 3.sch, CAN.sch, MCU.sch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]
2017-02-07 Completed part number, manufacturer, etc fields. Simulated analog conditioning
    [5v to 3.sch, BOM.csv, CAN.sch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]
2017-02-13 Added power integrations igbt driver interface board
    [250-1109-rev1.step, 75869104LF.step, B4B-PH-K-S.step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]
2017-02-13 Added power integrations igbt driver documents
2017-02-13 Added power integrations 3d assembly project
2017-04-19 Corrected phase current gain. More 3d models
    [5v to 3.sch, CAN.sch, MCU.sch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]
2017-06-16 Fix inverted diff signals
    [Power.sch, VESC-controller.sch, conditioning.sch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]
2017-06-17 Added individual temperature sensing for each half bridge and 2 pwm gpio with low side driver
    [5v to 3.sch, CAN.sch, GPIOs.sch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]
2017-06-30 Fixed power supply inductor footprints in the layout
    [5v to 3.sch, CAN.sch, GPIOs.sch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]
2017-07-06 Updated layout. DRC OK, moved silkscreen, bumped version to 0.2. Added portable 3d models
    [CAN.sch, VESC-controller.kicad_pcb]
2017-08-16 Add BOM
    [VESC-controller.xlsx]
2017-10-20 Added RC filter to FAULT line to prevent noise triggering it
    [5v to 3.sch, CAN.sch, GPIOs.sch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]
2017-10-20 Fix swapped differential signals in the interface board
    [1757268_06.step, 1923869_02.step, 1923872_02.step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]
2017-10-20 Added general documentation of the power integrations interface board
    [2SP0115T2A0_3D_v3.stp, BOM_Power_Integrations_interface.xlsx, INFINEON_FF600R06ME3.stp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]
2017-10-20 Not sure if I ran the DRC so lets push again with DRC checked.
    [VESC-controller.kicad_pcb]
2017-10-20 Add fabrication files for controller board
2017-10-20 Added fabrication files for IGBT driver interface from power integrations

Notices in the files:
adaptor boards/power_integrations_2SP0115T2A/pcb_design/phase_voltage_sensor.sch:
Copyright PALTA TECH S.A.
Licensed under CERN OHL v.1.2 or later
